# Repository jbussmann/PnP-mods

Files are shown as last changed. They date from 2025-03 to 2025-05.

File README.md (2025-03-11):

# PnP-mods

This repository is about my awesome little [LumenPnP](https://www.opulo.io/products/lumenpnp) desktop pick and place machine. Well actually, it belongs to my employer because I use it at work. I ordered the machine around a month after the release of v4 in fall 2024 because we were running out of time with a development project. It became increasingly apparent that no contract manufacturer would be able to assemble the boards we needed in the time we had left between end of development and start of testing. Also hand assembly was no option due to the high complexity of 60 PCBs with 240 placements and another 60 PCBs with 120 placements, with more than half of it being 0402 components. This is when I decided to take the plunge on desktop pick and place, in a slightly desperate attempt to make the deadline. The LumenPnP gave us a fighting chance to do so.

LumenPnP

This potato cam picture shows what I was working with at this time. During the roughly 10 days of machine time it took me to assemble all those boards, I not only learned a lot about the machine and [OpenPnP](https://openpnp.github.io), its accompanying control software, but I also run into several limitations and issues. Some are inherent to the approach of both hardware and software and therefore deeply baked into the design. Others are more like oversights or specific to my setup because as can be seen in the picture, space is one of the most limiting factor. The latter of those limitations and issues I tried and still am trying to improve on. This repository is a collection of my findings and my attempted improvements.

Many things are still work in progress or even just concepts I might or might not try at some point. Following are the topics I intend to address in the future.

### LumenPnP:
- optimize usable range of motion in the y-axis
- shrink nozzle rack
- improve passive strip feeders for 0402 components

### LumenPnP Feeder:
- improve ability to feed 1mm paper tape
- improve reliability with 0402 components
- improve packaging

### OpenPnP:
- simplify setting up a new job
- macro keyboard for "eyes off screen" machine control
- improved job planning and execution

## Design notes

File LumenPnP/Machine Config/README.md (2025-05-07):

# Machine Config: Draft

My attempt at a clean machine.xml for the LumenPnP, created from scratch and containing only settings applicable to all machines. It is intended to be used in conjunction with OpenPnP's Issues & Solutions and allowes users to skip the Welcome, Connect, Basics and Kinematics milestones and start right off targeting the Vision and Calibration milestones. This is still incomplete and untested, use at your own risk. Feedback is highly appreciated.

## Issue

There are maninly two ways to configure a LumenPnP:
- Starting from scratch and using Issues & Solutions  
This is what the developers of OpenPnP recommend. It is clean but also a lot of work. Additionally, it is unneccecary work because a lot of the resulting configuration is common to all LumenPnPs and can therefore be summarised in a machine.xml template. 

- Following the instrucions provided by Opulo
This provides a preconfigured machine.xml template however it is a messy one. It contains a lot of old and deprecated configuration fragments, as well as configuration data that is specific to the machine the template was originally created on. Furthermore, Opulo's instructions do all the calibration by hand. This is cumbersome, labor intensive and in many instances, there is a hands-off calibration procedure available which achieves the same goal, just faster and more accurate.

Both approaches are far from ideal and provide a suboptimal user experience.

## Proposed solution

To privide users with the best possible experience this solution provides a configuration file, purpose built from scratch. It aims at making the user calibration as short and smooth as possible while at the same time leveraging as many capabilities as possible of both the machine as well as the software. Starting from scratch, this configuration file does several things different than Opulo does in their own machine.xml
- Either solve or dismiss all solutions in Issues & Solutions until targeting the vision milestone.
- Clean up all gcode commands and make them match the suggestions by Issues & Solutions.
- Add calibration data to the nozzle tips themselves instead of hardcoding it in the pipeline stages.
- Reset all vision pipelines to default.
- Change from tool path to mederated acceleration and allow seperate tuning of all axes.

This allows the calibration procedure to improve considerably:
- Use of a one click solution to determine homing fiducial location, determine top camera orientation, roation angle and unit per pixle.
- Use of a one click solution to determine bottom camera location, orientation, ratation angle and unit per pixle.
- Use of advanced nozzle offset calibration solution to easily determine the nozzle offset as precise as the machine's motion system allows.
- Use of the built in nozzle tip runout calibration which leverages linked vision stages.
- Use of adaptive camera settling to minimize settling time.
- Use of nozzle tip background calibration to quickly and easily configure the camera exposure.
- Optional use of of the backlash calibration solution which provides a comprehensive reflection of the state of the motion system.

## Limitations

This config is created on and for OpenPnP 2.2 which was built in February 2025. It is also tested to work on newer builds but it is unlikely to work with older builds. This is due to a limitation in the xml parser, which is unable to handle elements in the config file, if they didn't exist in older versions of OpenPnP.

Unfortunately the OpenPnP 2.2 release was before this configuration file was finalized. Therefore, not all bugs that came up during the creation of the config could be fixed in time. At least one remains in the  2.2 release and was only fixed later on:

- The LumenPnP has no secondary fiducial, therefore the associated calibaration in Issues & solutions is to be dismissed. Due to a bug, dismissing this solution through the UI is impossible and was therefore dismissed by manually editing the configuration file. Due to the same bug, users are also unable to reopen this solution, in case they wish to use a custom made secondary fuducial. To reopen this solution either update to a newer build of OpenPnP or manuall remove the line `<string>831b760f63cd9d1b93a457157a4f8c366aa0cf33</string>` from the config file under `dismissed-solutions`.
- Camera settings getting lost.

## Implementation

There will be a video about how to progress through the few steps from the state that the config file provides to picking and placing the first parts. For those who don't want to wait or prefer text based instructions, here is a preliminary list of the steps that remain to be completed.

While targeting milestone vision:
- Accept the enable and home machine solution  
Relevant Opulo docs: [Homing Fiducial](https://docs.opulo.io/openpnp/calibration/4-homing-fiducial/)
- Manually load nozzle tips NT045 and NT24  
Relevant Opulo docs: [Mounting Nozzle Tips](https://docs.opulo.io/openpnp/calibration/5-mm-per-pixel/#mounting-nozzle-tips)
- Manually test the vacuum system and setup the thresholds  
Relevant Opulo docs: [Vacuum Part Detection](https://docs.opulo.io/openpnp/calibration/10-vacuum-sensor/)
- Accept the set primary fiducial solution, use a feature diameter of 92px  
Relevant Opulo docs: [Setting Homing Fiducial Location](https://docs.opulo.io/openpnp/calibration/4-homing-fiducial/#setting-homing-fiducial-location) and [Top Camera Calibration](https://docs.opulo.io/openpnp/calibration/5-mm-per-pixel/#top-camera-calibration)
- Accept the enable visual homing solution  
Relevant Opulo docs: [Test Fiducial Homing](https://docs.opulo.io/openpnp/calibration/4-homing-fiducial/#test-fiducial-homing)
- Accept the use adaptive settling solution for the top camera
- Accept the nozzle N1 offset for primary fiducial solution
- Accept the nozzle N2 offset for primary fiducial solution  
Relevant Opulo docs: [Nozzle Offset](https://docs.opulo.io/openpnp/calibration/6-nozzle-offset/)
- Accept the bottom camera initial calibration, use feature diameter of 12px and disable auto focus  
Relevant Opulo docs: [Bottom Camera Position](https://docs.opulo.io/openpnp/calibration/7-bottom-camera-position/) and [Bottom Camera Calibration](https://docs.opulo.io/openpnp/calibration/5-mm-per-pixel/#bottom-camera-calibration)
- Accept the use adaptive settling solution for the bottom camera  
- Accept the milestone vision

While targeting milestone calibration:
- Dismiss or accept the backlash compensation for x and y axes
- Manually set the primary fiducial location to where the hole punch is
- Accept the N1 precise nozzle offset solution
- Manually readjust primary fiducial location if necessary
- Accept the N2 precise nozzle offset solution
- Manually reset the primary fiducial location to homing fiducial
- Manually enable nozzle tip calibration on all six nozzle tips
- Accept nozzle tip background calibration for all loaded nozzle tips
- Acceept the milestone calibration

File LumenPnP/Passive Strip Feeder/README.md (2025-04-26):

# Passive Strip Feeder

A much improved version of the popular Menlu strip feeder, originally designed by ERIK3DP. It allows the LumenPnP to easily use small parts and thin plastic tape without the headache of parts jumping all over the place.

8mm and 12mm feeder array

## Issue

The strip feeders provided by Opulo to accompany the LumenPnP are of a very simplistic design. This is a compromise and leads to limitations in their application. The main issue of these stock feeders is their inability to fixate components tape in the vertical direction. Their fixed geometry works adequately with thick tape but because they have no moving parts to compensate for changes in tape thickness, they are especially problematic for parts in thin tapes like 0402 components and plastic tapes. This is because it is almost impossible to use such parts as simply touching the tape can send all the parts flying that are no more protected by the cover film. The stock feeders also have limitations when used with extremely thick tape, as this tape can get stuck and buckle due to excess friction, when trying to slide it into the feeder.

## Proposed Solution

To solve the issue of loose tapes, the feeder has to vertically fixate the tape. One simple way to do this is by a spring loaded mechanism beneath the tape, pushing it upwards. The Menlu strip feeder by [ERIK3DP](https://www.printables.com/model/885928-menlu-strip-feeder-8mm12mm-for-lumenpnp) is a very popular example of such a feeder system. The OpMenlu strip feeder by [ruudwes](https://www.printables.com/model/1147285-opmenlu-stripfeeder-for-the-lumenpnp) is based on the original Menlu feeder but in many ways improved and further adapted to the LumenPnP. 

The OpMenlu strip feeder system consists of two parts, a stationary base, bolted to the machine table, as well as a movable slider. Although this feeder has a lot of potential, it still has several shortcomings. When asked to improve on these, the author of the OpMenlu feeder deemed some of the suggested improvements unnecessary or impossible to solve and did only offer to share the parametric model, when it was already too late.

As a consequence, the feeder presented here is completely remodeled from scratch. It is heavily inspired by the many good ideas of the Menlu and OpMenlu designs but is at the same time in many aspects massively improved:

- The tape's surface is now 10 mm above the staging plate, where the top camera's focal plane, the PCBs and all other feeders are. This is more than 1 mm lower than before.
- The base has the full array of mounting holes available for maximum flexibility.
- All mounting holes are easily accessible from above without the need to remove the slider. This is especially useful if multiple sliders are mounted in a row, which the design is intended to be used for.
- The slider wall supporting the sprocket holes is now rectangular and much thicker at the point where it connects to the slider body. This makes it much less likely to break off e.g. when removing potential support material.
- The slider wall opposite of the sprocket holes on the other hand is now thinner. This is to accommodate tapes with very large components and consequently very thin tape edges.
- The 8 mm feeders are available in compact arrays of 4 and 10 rows with a pitch of 10 mm. They occupy the same area as 3 or 7 rows of the standard design with 15 mm row pitch would, thus making this design up to over 40% more space efficient.
- This modification also contains a wider 12 mm version of the same design, as these wider tapes suffer from the same issue.
- The overall design is stripped of all unnecessary features and improved for 3D printing.

As this comprehensive list demonstrates, all shortcomings of the OpMenlu design were easily solvable. At the same time the mushroom style caps, used to guide the cover tape, were deemed only marginally useful and were therefore removed in the process of making the design more compact. 

## Implementation

There are subfolders for the 8 and 12 mm designs, each containing FreeCAD models of both the base of the feeder and its corresponding slider. Additionally there are STL-files for 3D printing of the slider and the base, latter of which in different numbers of rows. The prints should turn out well even when printed with 0.2 mm layers. There are however two critical areas of the model:

- The slider requires bridging at a height of 2.5 mm. With the appropriate settings, this can easily be printed without support material. If in doubt, enable support.
- There is a ramp. On the slider it's between 4.5 and 6.5 mm height and on the base it's between 3.0 and 3.8 mm. Printing this with 0.2 mm will be very rough and has the potential to make the mechanism unusable. One way to solve this is to print either the base or the slider (one of both is enough) with 0.10 to 0.12 mm layer height. A more elegant solution is to use a layer height modifier (as supported e.g. by the Prusa slicer and Bambu Studio) to reduce the layer height to between 0.10 and 0.12 mm only in the range where this ramp is. Again, doing this on only one of both parts should be enough.

After printing the parts, test fit the slider into the base. If it gets stuck, cut or file away whatever excess material there is. If the fit is good, use a suitable rubber band/ring to mount the parts together.

In its shortest position, the required rubber band is roughly 32 mm long (10 mm diameter), while in its longest position it's roughly 56 mm long (18 mm diameter). To exert an uniform force over the the whole range, the rubber needs to be shorter than the shortest position and be able to stretch to at least 3 times its original length. A thin and soft band with around 6 mm diameter works well. Springs might work as well but are not tested. When needed, adapt the model and move the pins to fit the requirements.

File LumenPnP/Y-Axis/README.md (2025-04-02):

# Y-Axis Optimisation

A modification optimising y-axis travel to increase the usable area of the machine in triple staging plate configuration by almost 10%. It involves replacing the front legs with newly printed ones, slightly rearranging the staging plates and updating the configuration of OpenPnP to reflect the changed geometry.

## Issue

The image below shows the machine in it's default configuration, drawn to scale. It shows the build plate as well as  the staging plate and both rows of LumenPnP Feeders. Additionally it shows in grey the optional 3rd staging plate in the back.

Machine Table before

Overlaid are multiple rectangles, outlining the usable range of the different tools on the machine head. Green marks the area which can be reached by the camera. The blue rectangle marks the area reachable by both nozzles and the red areas are only accessible by one of the nozzles.

Looking at his image, the issue should become rather clear: there is an area approximately 30 mm deep, spanning across the whole width in the back of the machine, where none of the nozzles can reach. This is wasted area of the 3rd staging plate and as this simple modification demonstrates, it is wasted for no reason.

## Proposed Solution

The inaccessible area in the back of the machine can easily made useable by moving the staging plates 35 mm closer to the front of the machine. While 30 mm would be enough, the additional 5 mm cover potential variances for example in the assembly process of the machine. To retain all functionalities of the machine and to not break compatibility, the front feeder rail needs to move by the same amount for the feeders not to collide with the build plate. This in turn requires modifications to the front legs, as these define the position of this rail. This is the main content of this modification. The following image illustrates the new situation after the modification.

Machine Table after

As can be seen, the nozzles (blue and red) can now reach all the way to the rear edge of the third staging plate and the front feeder pick window is still within reach of nozzles and camera. The nozzles can even reach as far as a fourth staging plate in the front, added in grey. After all, the y-axis travel limit of 487 mm exceeds the length of four build plates, which are a total of 480 mm long. It is thus not only possible but also practical (see the picture in the top level README of this repo) to add a fourth staging plate in the front.

Such a fourth staging plate can for example be used to support another full row of strip feeders. There are however some limitations to this practise. Because the front legs are in the way, a potential fourth staging plate needs a cut-out that is 20 mm wide and 46 mm long, to allow room for the front legs. It's also not possible to use the standard build plate foot, as it collides with the front feeder blades by only a few millimetre. Modification of the foot or the mounting hole in the plate is needed. Additionally, a potential fourth build plate needs cut-outs for as many LumenPnP Feeders (or others) as there are to be mounted onto the front feeder rail. The last limitation is that strip feeders mounted to this staging plate are only about half way through in the range of the camera. In order to use their full length, they need to be configured as tray feeders in OpenPnP, or something else that doesn't rely on vision. If during setup of the strip feeders the necessary care is taken, this is proven to not only work flawless but also considerably faster.

There are multiple ways to accommodate the moved front feeder rail and staging plates. This solution is limited to only modifying the front legs, touching the least number of machine parts and changing the configuration of OpenPnP. Doing this severely limits the scope of the modification to a local optimum and leaves many more potential optimizations untouched. It is chosen to maximise the accessibility of the modification for as many users as possible. Other options would be to move the front feeder rail by a shorter distance because the frame of the LumenPnP Feeder could be made quite a bit shorter, as demonstrated in [this](https://github.com/jbussmann/PnP-mods/tree/draft_feeder-frame/LumenPnP%20Feeder/Feeder%20Frame) proposed modification. However, such a change would break compatibility to the existing feeders as they are sold by Opulo. Additional optimization can be found by overhauling the design of the head assembly and parts of the gantry. This however is outside of the scope of this simple modification as it would involve printing many new parts, almost completely disassembling the machine and potentially even changing the controller firmware.

## Implementation

The core of this modification is a pair of modified front feet. They are remodeled from scratch, according to the original models, which turned out to be unworkable due to their complexity. The new model is stripped of all non-functional features and is thus much lighter in terms of the feature tree. It comes as individual STL-files, for those who just want to print it and as a FreeCAD multi-body part, for those who want to make further modifications. There are also two SVG-files with the outline of a fourth staging plate, in case someone wants to have this too. One is a full staging plate and the other one is split, to accommodate 5 LumenPnP Feeders in the centre. Both feature the necessary cut-outs around the front feet and are intended to be used for cutting or milling. If the intention is to use PCBs, Opulo's [PCB design file](https://github.com/opulo-inc/lumenpnp/blob/main/pnp/pcb/staging-plate/staging-plate.kicad_pcb) is a better starting point.

A word of warning before diving in: doing this modification messes with the coordinate system, because it moves the homing fiducial. As a result, all precise x and y coordinates become invalid and need to be checked and potentially updated. This applies to the tool changer positions but also to all feeder positions. Keep this in mind before proceeding and maybe save the following steps for a period of machine downtime.

- First of all, print the modified front feet. They have the same requirements as the original parts, print settings can be found [here](https://docs.opulo.io/byop/mechanical-assembly/1-printing-parts/). 
- Remove the front feeder rail from the machine, together with the angle-brackets.
- Use this rail to test fit all pockets and slots of the new 3D printed parts. Remove potential scrapes and bridging residues.
- Remove both of the original front feet from the machine.
  - Remove the y-axis striker.
  - Loosen both y-axis idler pulleys and remove both idler pulley arms.
  - Now the feet themselves can be removed.
- Remove the angle-brackets form the front feeder rail. Due to the changed mounting of the rail, they will go somewhere else.
- Transfer all mounting elements form the original to the new 3D prints. Do the same with the feet extensions.
- On the left foot, don't forget the threaded insert for the y-axis striker.
- With all that done, assembly can begin. This part is a bit cumbersome if done as a retrofit instead of with a fully disassembled machine.
  - Start by slotting both feet onto the front feeder rail.
  - Carefully slot the assembly onto the lower y-axis rails.
  - Insert the top y-axis rails into the feet and continuously push everything into place.
  - With everything firmly in place, tighten all the bolts.
  - Remount both y-axis idler pulley arms and the idler pulleys.
  - Remount the y-axis striker.
- As a last step mount the angle-brackets, now on top of the front feeder rail.

With all these steps done, the most difficult part is already done and now comes the fun part, which actually makes a difference: loosen all staging plates on the machine and realign them 75 mm away from the front feeder rail. This is identical to the initial assembly and can be done by using the supplied jig.

Now open OpenPnP and adjust the position of the homing fiducial, the bottom camera and everything else that is bolted to the build/staging plate(s). This would be a good opportunity to update to the official release of OpenPnP 2.2 or even the most recent test build of OpenPnP 2.3 and try an improved machine.xml from [here](https://github.com/jbussmann/PnP-mods/tree/draft_machine-config/LumenPnP/Machine%20Config). Test and make sure that everything still works and enjoy the now almost 10% larger usable machine area, compared to the standard triple build plate setup. Or a whopping 45% compared to the standard triple plate setup, in case a fourth plate is added.

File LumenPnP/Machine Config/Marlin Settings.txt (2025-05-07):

> M503
echo:; Linear Units:
echo:  G21 ; (mm)
echo:; Temperature Units:
echo:  M149 C ; Units in Celsius
echo:; Steps per unit:
echo:  M92 X320.00 Y320.00 Z40.00 A4.44 B4.44
echo:; Max feedrates (units/s):
echo:  M203 X1500.00 Y1500.00 Z500.00 A50000.00 B50000.00
echo:; Max Acceleration (units/s2):
echo:  M201 X10000.00 Y10000.00 Z10000.00 A10000 B10000
echo:; Acceleration (units/s2) (P<print-accel> R<retract-accel> T<travel-accel>):
echo:  M204 P3000.00 R3000.00 T3000.00
echo:; Advanced (D<min_segment_time_us> S<min_feedrate> T<min_travel_feedrate> J<junc_dev>):
echo:  M205 D20000.00 S0.00 T0.00 J0.01
echo:; Home offset:
echo:  M206 X0.00 Y0.00 Z0.00 A0.00 B0.00
echo:; Stepper driver current:
echo:  M906 X800 Y1000 Z800 A200 B200
echo:  M906 I1 Y1000
echo:; Driver stepping mode:
echo:  M569 S1 Z A B
echo:  M569 S1  A
echo:  M569 S1  B

> M906
X driver current: 800
Y driver current: 1000
Y2 driver current: 1000
Z driver current: 800
I driver current: 200
J driver current: 200

> M211
M211 S1 ; ON
Min:  X0.00 Y0.00 Z0.00 A0.00 B0.00   Max:  X433.00 Y487.00 Z63.00 A720.00 B720.00

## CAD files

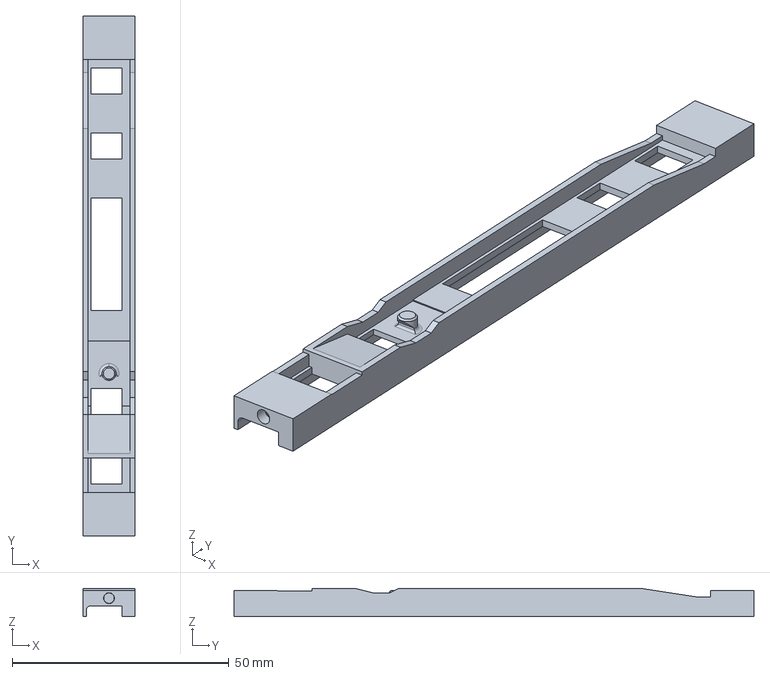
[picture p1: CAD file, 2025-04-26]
LumenPnP/Passive Strip Feeder/12mm/OpMenlu-slider-12mm.FCStd
12.0 x 120.0 x 6.50 mm

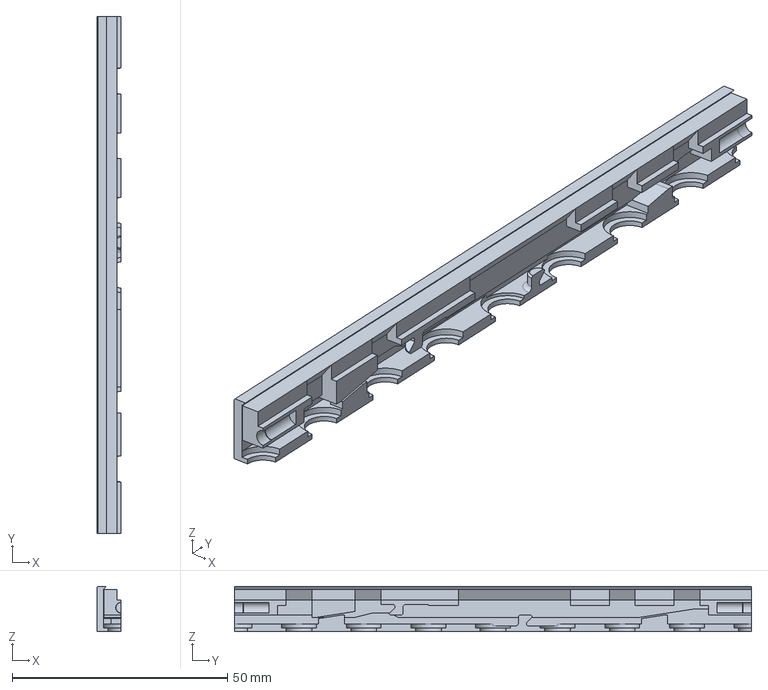
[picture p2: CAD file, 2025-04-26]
LumenPnP/Passive Strip Feeder/8mm/OpMenlu-base-1x8mm.FCStd
5.60 x 120.0 x 10.5 mm

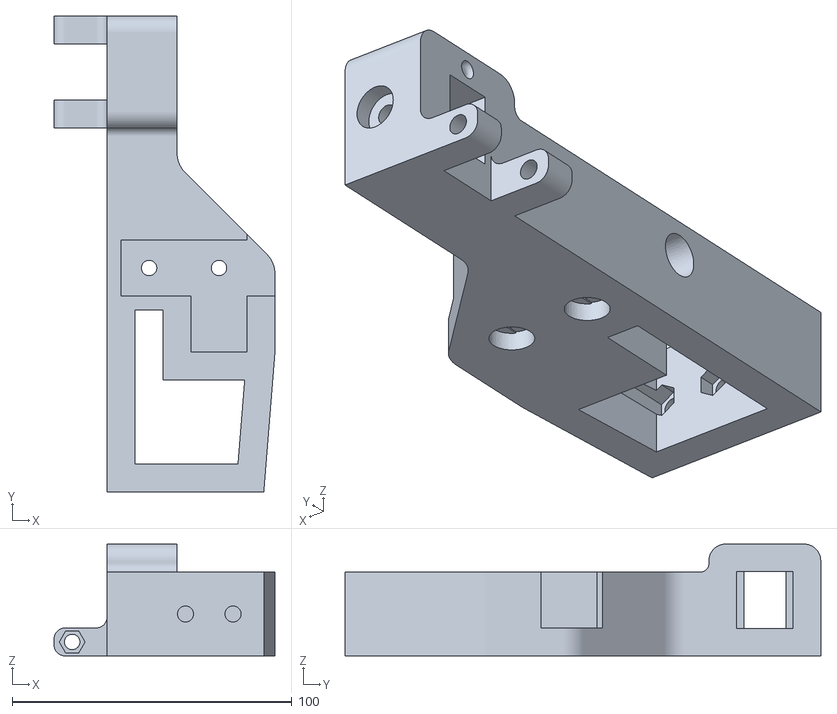
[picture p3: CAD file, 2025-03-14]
LumenPnP/Y-Axis/front-legs-left.stl
79.0 x 170.0 x 40.0

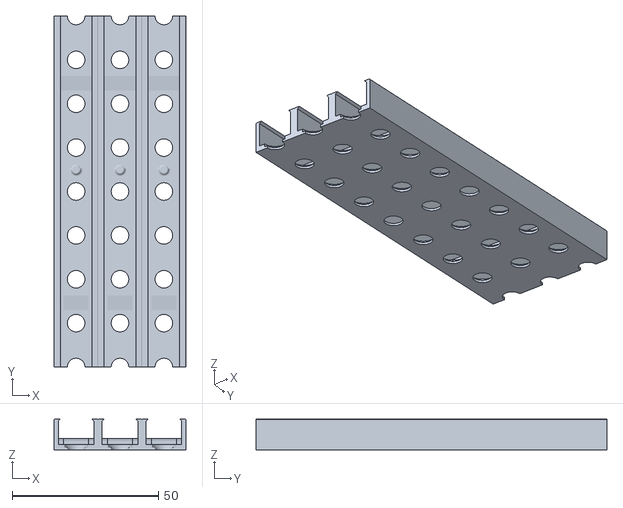
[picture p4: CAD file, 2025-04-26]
LumenPnP/Passive Strip Feeder/12mm/OpMenlu-base-3x12mm.stl
45.0 x 120.0 x 10.5

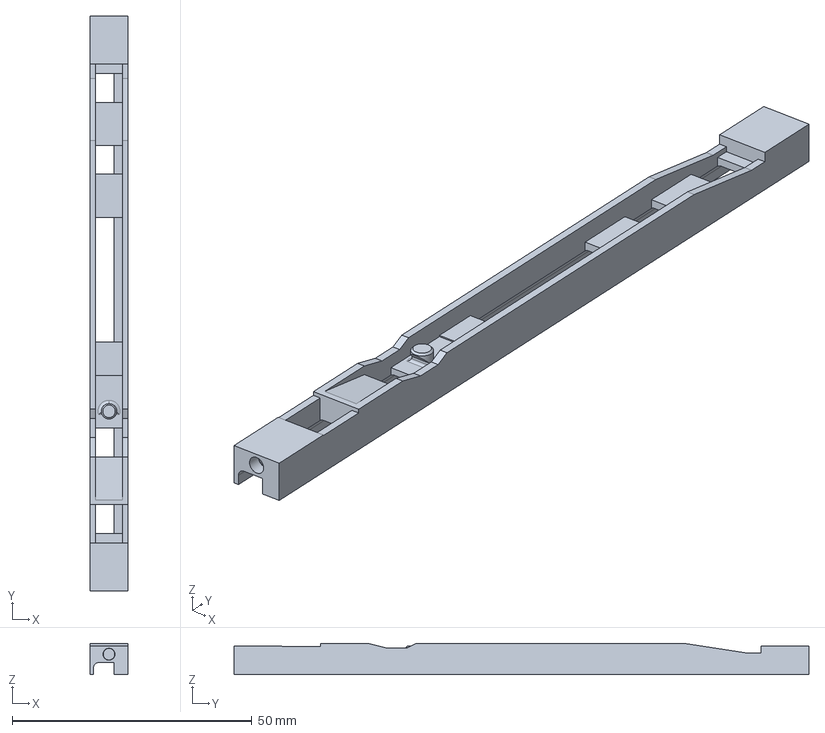
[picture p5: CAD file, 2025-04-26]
LumenPnP/Passive Strip Feeder/8mm/OpMenlu-slider-8mm.FCStd
8.00 x 120.0 x 6.50 mm

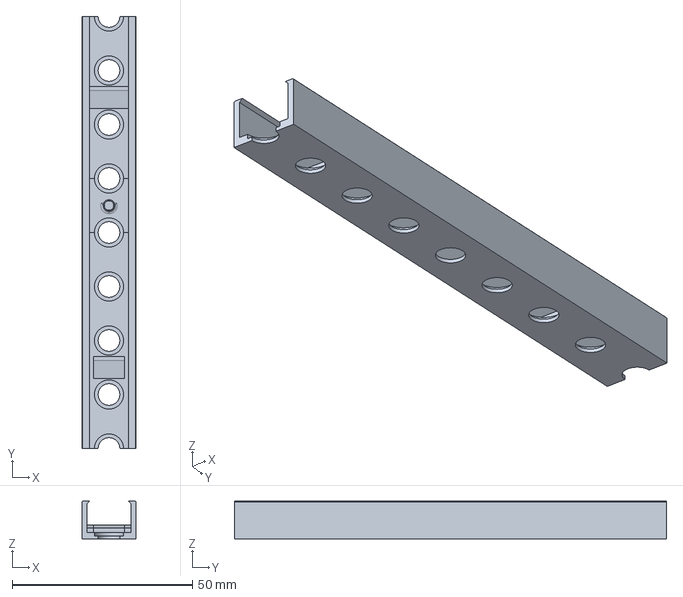
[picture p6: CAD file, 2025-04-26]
LumenPnP/Passive Strip Feeder/12mm/OpMenlu-base-1x12mm.FCStd
15.0 x 120.0 x 10.5 mm

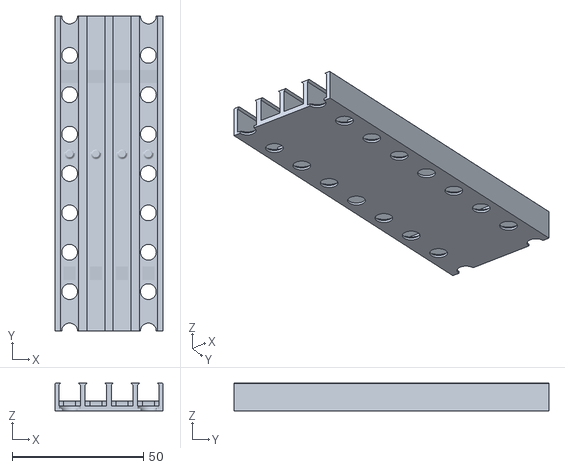
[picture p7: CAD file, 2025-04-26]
LumenPnP/Passive Strip Feeder/8mm/OpMenlu-base-4x8mm.stl
41.2 x 120.0 x 10.5

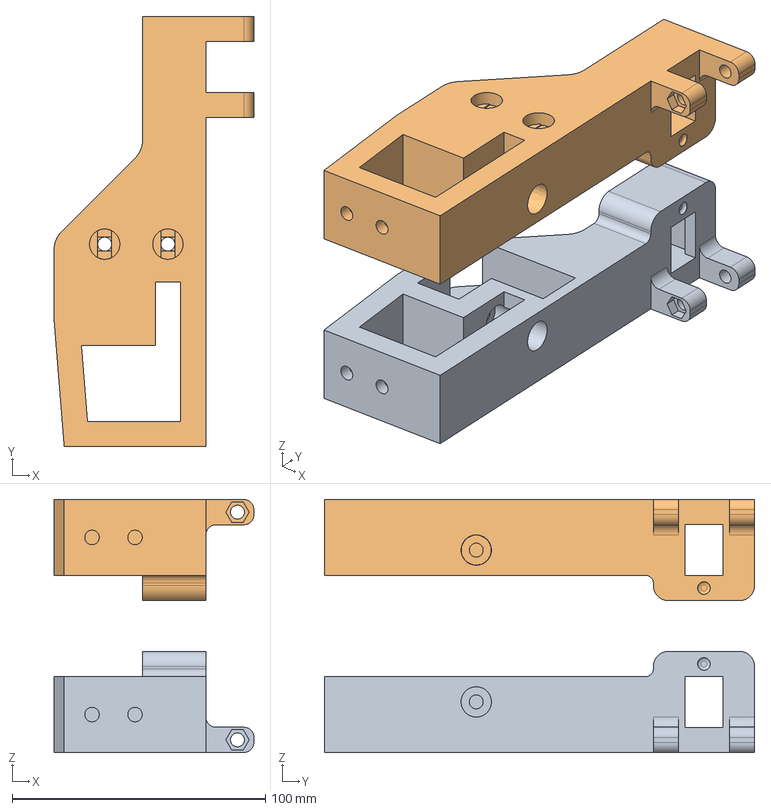
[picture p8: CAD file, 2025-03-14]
LumenPnP/Y-Axis/front-legs.FCStd
79.0 x 170.0 x 100.0 mm
RightLeg
LeftLeg

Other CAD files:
LumenPnP/Y-Axis/front-legs-right.stl
LumenPnP/Passive Strip Feeder/12mm/OpMenlu-base-1x12mm.stl
LumenPnP/Passive Strip Feeder/12mm/OpMenlu-slider-12mm.stl
LumenPnP/Passive Strip Feeder/8mm/OpMenlu-base-1x8mm.stl
LumenPnP/Passive Strip Feeder/8mm/OpMenlu-slider-8mm.stl

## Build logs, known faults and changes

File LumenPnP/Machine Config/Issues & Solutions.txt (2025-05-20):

Description: use demo simulation machine and choose nozzle configuration

Executed tasks:
accepted: create nozzles for this head
manually: remove feeders, parts and packages from simulation machine except fiducials
manually: remove existing nozzle tips (so they are assigned uniform IDs)
manually: create CP40 nozzle tip set (use prefix NT for nozzle tip)
-----------------
Milestone Welcome
=================

Description: connect to controllers and cameras

Executed tasks:
manually: remove bottom cam and create new up-looking cam (get rid of some preconfigs)
manually: remove topcam and create new down-looking cam (get rid of some preconfigs)
manually: select real USB cameras from the respective dropdowns
accepted: replace Gcode driver with real driver
manually: select Gcode driver comms type and serial port
accepted: detect firmware
accepted: change serial flow control
-----------------
Milestone Connect
=================

Description: configure machine axes, motion, vacuum and light switching

Executed tasks:
accepted: 5x axis letter missing
accepted: 4x top camera axis assignment missing
accepted: 2x enable switch linear/rotational
manually: rearrange and rename axes (small letters, C1->a, C2->b ect.)
manually: remove all machine actuators and create LED and PhotonFeeder actuators
manually: configure LED actuator on both cameras
manually: remove all head actuators and create VAC1 and VAC2 actuators
manually: configure vacuum and sensing actuators on both nozzles
manually: restart OpenPnP for I&S to pick up the new configuration
manually: configure all gcode according to gcode file
dismissed: H1 is missing pump actuator
----------------
Milestone Basics
================

Description: define save z, soft limits, motion control model, feed-rates, accelerations etc.

Executed tasks:
accepted: home machine
manually: configure z1 homing coordinate and z2 mapping points
accepted: 2x enable dynamic safe z
accepted: 2x set safe z
dismissed: 2x unconventional z axis (cannot be dismissed: potential bug)
manually: set and enable soft limits for x and y
manually: set and enable soft limits for z1 (very important for all positive z axis!)
manually: set nozzle tip change location for both nozzles
manually: set individual feed rate and acceleration by axes
accepted: 2x align nozzle rotation with part
accepted: 2x enable wrap around
accepted: enable ModeratedConstantAcceleration
accepted: remove diver maximum feed rate
--------------------
Milestone Kinematics
====================

Description: setup camera and computer vision

Executed tasks:
manually: set all camera settings to default, except sharpness to 0
accepted: 2x suspend camera preview during machine tasks
dismissed: 2x enable auto camera view
dismisses: 2x calibrate static white balance
manually: add compatible and loaded nozzle tips
----------------
Milestone Vision
================

Description: calibrate the machine for precise motion and vision

Executed tasks:
manually: add nozzle tip calibration data
manually: 
---------------------
Milestone Calibration
=====================

configure feeders
solve other production related issues
--------------------
Milestone Production
====================

advanced features for faster and more automatic machine
------------------
Milestone Advanced
==================
accepted: switch to advanced motion planner

Potential bugs:
- unconventional z axis: undismissable -> fixed
- secondary fiducual: error at dismiss
- after bottom cam calib: no cam found

Potential pitfalls:
- Nozzle offset: no mention of nozzle tip for capturing Z

To do:
- Finish vacuum setup (dwell times, thresholds etc.)
- preemptive feeding (actuator coordination, async driver)
- stock bottom vision vs default machine vision

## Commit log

2025-03-14 add y-axis modification
    [front-legs-left.stl, front-legs-right.stl, front-legs.FCStd]
2025-04-26 add passive strip feeder modification
    [OpMenlu-base-1x12mm.FCStd, OpMenlu-base-1x12mm.stl, OpMenlu-base-1x8mm.FCStd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]
2025-05-07 reset camera settings
2025-05-07 add nozzle tip calibration data
2025-05-07 add suspend camera preview
2025-05-07 add compatible and loaded nozzle tips
2025-05-07 limit part diameter to nozzle shade
2025-05-07 add led actuation at enable and disable
2025-05-07 split LED actuator
2025-05-07 dismiss secondary calibration fiducial
2025-05-07 dismiss advanced bottom camera calibration
2025-05-07 increase acceptable backlash tolerance
2025-05-07 configure all front feeder slot locations
2025-05-07 remove nozzle tips
2025-05-07 add marlin settings
2025-05-07 add proper IDs to head and nozzle
2025-05-20 switch to advanced motion planner
